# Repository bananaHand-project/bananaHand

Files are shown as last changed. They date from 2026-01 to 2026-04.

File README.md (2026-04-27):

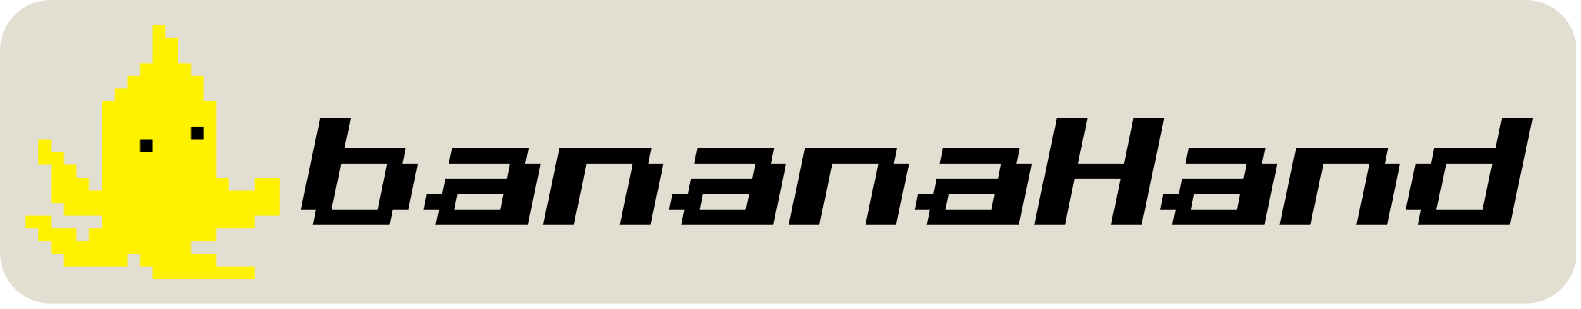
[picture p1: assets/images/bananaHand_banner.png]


---

**BananaHand** is an open-source 16 DOF/6 DOA humanoid hand designed for physical AI research and deployment on light-weight robot arms.

Hand teleop and telemetry demo

BananaHand features human-like proportions with no fore-arm, up to 4lb payload capacity, integrated palm and finger tip FSR based force sensing, and a low BOM cost of $900USD.

With the project being open-source as a top priority, all resources used in the creation are freely available and open-source themselves (KiCad, OnShape, Foxglove, Embassy-rs, etc.).

*We're in continuous development and actively seeking contributors, research partners, and company collaborators to shape the next generation of practical humanoid systems. Ready to join the future of open-source robotics?*

## Repo Structure

- [`docs/`](./docs/) contains build instructions, getting started guide, and more.
- [`firmware/`](./firmware/) contains the code that runs on the bananaHand main board.
  - [`firmware/primary-g474/`](./firmware/primary-g474/) contains the firmware run on the primary MCU (stm32g474).
  - [`firmware/sensing-c071/`](./firmware/sensing-c071/) contains the firmware run on the sensing MCU (stm32c071).
  - [`firmware/common/`](./firmware/common/) contains code used by both MCUs.
  - [`firmware/experiments/`](./firmware/experiments/) contains code used in the development of the hand.
- [`hardware/`](./hardware/) contains both electrical and mechanical CAD models, BOMs, and detailed descriptions.
- [`software/`](./software/) contains ROS and Foxglove implementations.

---
***We can't wait to see what you grasp!***

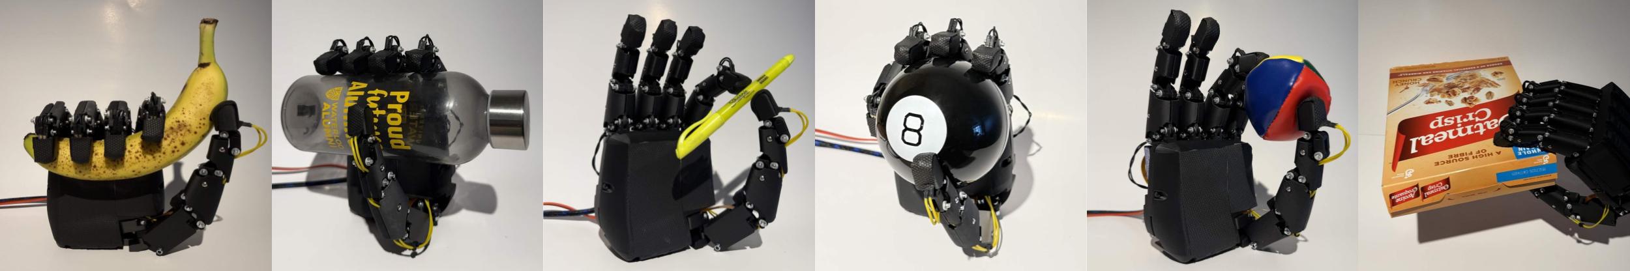
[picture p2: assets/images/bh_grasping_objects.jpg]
bananaHand grasping objects


Made with ❤️ in 🇨🇦 at 🪿.

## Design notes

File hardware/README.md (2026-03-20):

# Hardware

This folder contains files and information regarding CAD, PCB, BOM, and manufacturing files.

## CAD
The CAD for BananaHand is publicly hosted on Onshape for users to access, copy, and export. The link to the Onshape can be found below:
https://cad.onshape.com/documents/f31bf6b3693af5bdccd83d8c/w/d3ff086828b5bf32fd810037/e/c279298b7ecf651fc2ff6194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

## BOM and Assembly Guide
The BananaHand Bill of Materials can be found on Google Sheets through the following link: https://docs.google.com/spreadsheets/d/1iI2emtTwuQCvzfNIwKDL3XGDNOlOl9XfeF24zAXsmqI/edit?usp=sharing

The assembly guide for BananaHand can be found in the resources folder.

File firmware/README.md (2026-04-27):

# Firmware

Firmware for the BananaHand main board lives here. The board uses two MCUs:

- `stm32g474` (primary): communication, control loops, motor drive outputs.
- `stm32c071` (sensing): force sensor acquisition and streaming to the primary MCU.

## High-Level Architecture

- [`primary-g474/primary`](./primary-g474/primary): production firmware for the primary controller.
- [`sensing-c071`](./sensing-c071): production firmware for force sensing.
- [`common`](./common): shared packet definitions and encoding helpers.
- `experiments/`: one-off firmware targets used during bring-up and feature exploration.

## How It Works

1. The C071 samples 10 FSR channels (200 Hz), packs 12-bit readings with a checksum (`banana_hand_common::ForceDataPacket`), and sends them over UART to the G474.
2. The G474 runs concurrent Embassy tasks for host command RX (`USART3`), telemetry TX (`USART3`), force packet RX from C071 (`USART2`), position ADC sampling (`ADC1`), and current ADC sampling (`ADC2`).
3. A 200 Hz control loop on the G474 reads the latest shared snapshots and runs either `Position` mode (PID on actuator position) or `Force` mode (PID on force feedback where available).
4. Motor commands are converted to PWM outputs for the H-bridge channels.
5. Telemetry is sent to the host as combined position + force + current frames.

Current host communication is UART (`115200`) with COBS framing and a simple additive checksum on payloads.

## Build/Flash

Primary MCU (`STM32G474`):

```bash
cd firmware/primary-g474/primary
cargo run --release
```

Sensing MCU (`STM32C071`):

```bash
cd firmware/sensing-c071
cargo run --release
```

Both targets are configured to use `probe-rs run` in their local `.cargo/config.toml`.

## TODOs

- Add firmware support for CAN and half-duplex RS485 (board hardware already exposes both).
- Improve message passing robustness (stronger CRCs, sequence IDs with ACK/NACK or retries, and host heartbeat/command timeout fail-safe behavior).
- Remove unnecessary COBS usage (evaluate simpler framing on fixed-size links and delete stale code paths such as `sensing-c071/src/protocol.rs`).
- Tighten C071->G474 framing robustness (current stream has no explicit delimiter; resync is byte-sliding on checksum failure).
- Centralize protocol definitions so firmware and ROS bridge cannot drift.
- Create actuator/sensor calibration procedure (per-channel scaling and nonlinearity compensation).
- Add support for HRTIM triggered ADC conversions to `embassy-rs` so current feedback for protection and control (overcurrent limits, stall detection, fault handling).

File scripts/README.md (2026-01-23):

# Scripts

Utility scripts (calibration, flashing, logs).

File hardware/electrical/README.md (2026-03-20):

# Electrical

The electrical system for bananaHand is built around the main board. The main board is responsible for the following functions: communication with the controlling device, motor control, and FSR sensing. A simplified block diagram describing the main board can be seen below. It requires a single +12V 24W input source and exposes UART, CAN bus, and half-duplex RS485 options for interfacing. Depending on the device you are trying to interface with, a buck converter may be needed to drop your source voltage down to the required 12V.

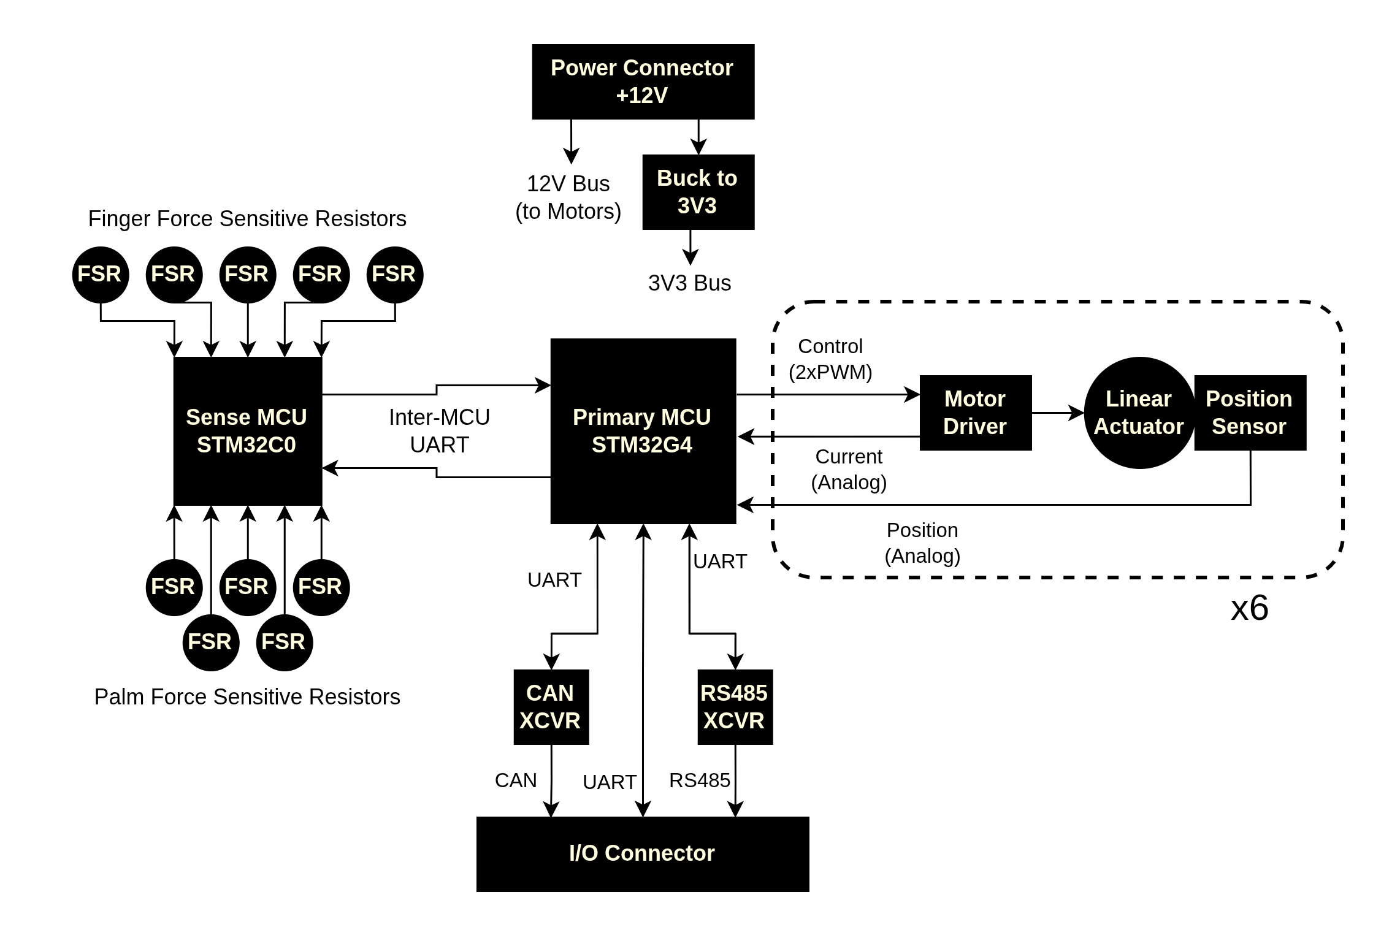
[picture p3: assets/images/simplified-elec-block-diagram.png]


## Main Board

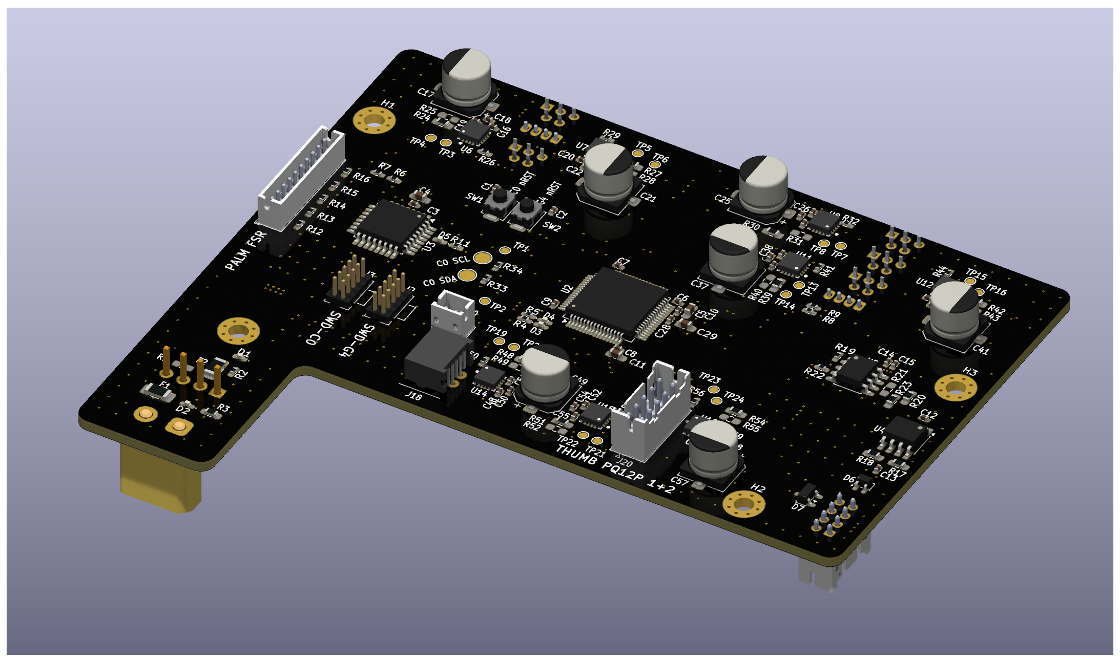
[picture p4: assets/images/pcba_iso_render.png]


The main board has the following sub-circuits:

- **Micro-controllers**: There are two MCUs on the main board. The first is the stm32g474, responsible for communication with the upstream device and motor control. The second micro-controller is the stm32c071, which acts as a "smart" ADC, filtering and forwarding force readings to the stm32g4.
- **Power stage**: Basic fuse protection, and a MPM3610 buck converter for 12V -> 3V3 for logic level ICs
- **Motor driving**: There are eight DRV8876 motor driver circuits for the [PQ12P](https://www.actuonix.com/pq12-30-12-p). The driving circuits are controlled and motor positions are read by the stm32g474 micro-controller.
- **Force sensing**: Simple linear voltage divider circuits are used to interface with the force sensitive resistors. Their voltages are read by the 2nd micro-controller on board the stm32c071
- **Communication interfaces**: There are three communication interfaces exposed by the board: CAN Bus, UART, and half-duplex RS485.

### Schematic

A full PDF of the schematic can be found in `bh_main_board/bananaHand_main_board_sch.pdf` or linked [here](./bh_main_board/bananaHand_main_board_sch.pdf).

### Layout

**Four layer:** Sig, GND, GND/PWR, Sig

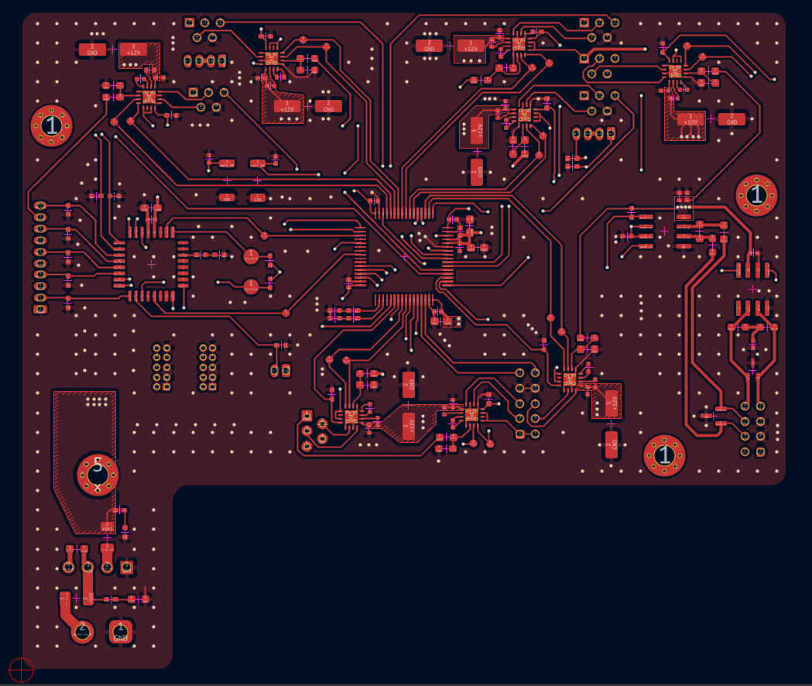
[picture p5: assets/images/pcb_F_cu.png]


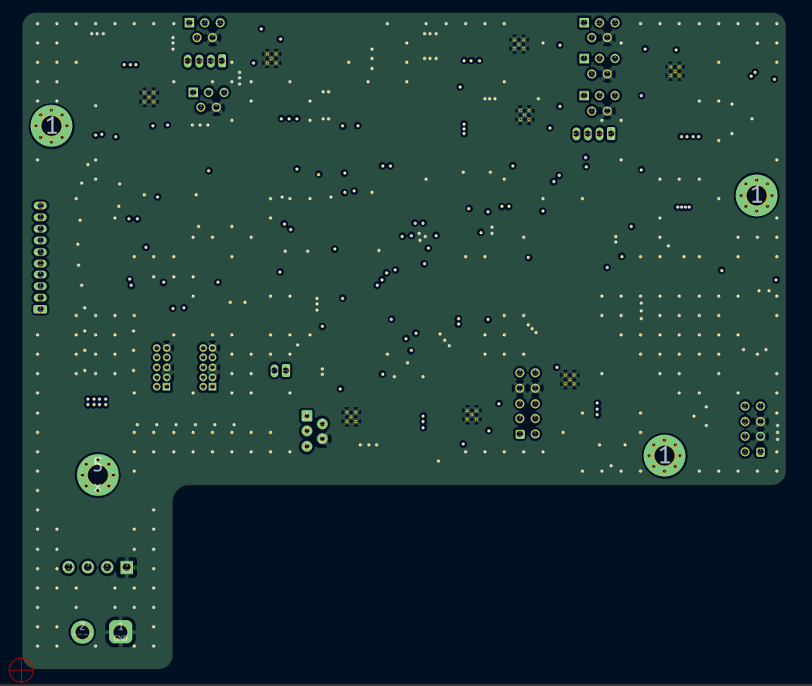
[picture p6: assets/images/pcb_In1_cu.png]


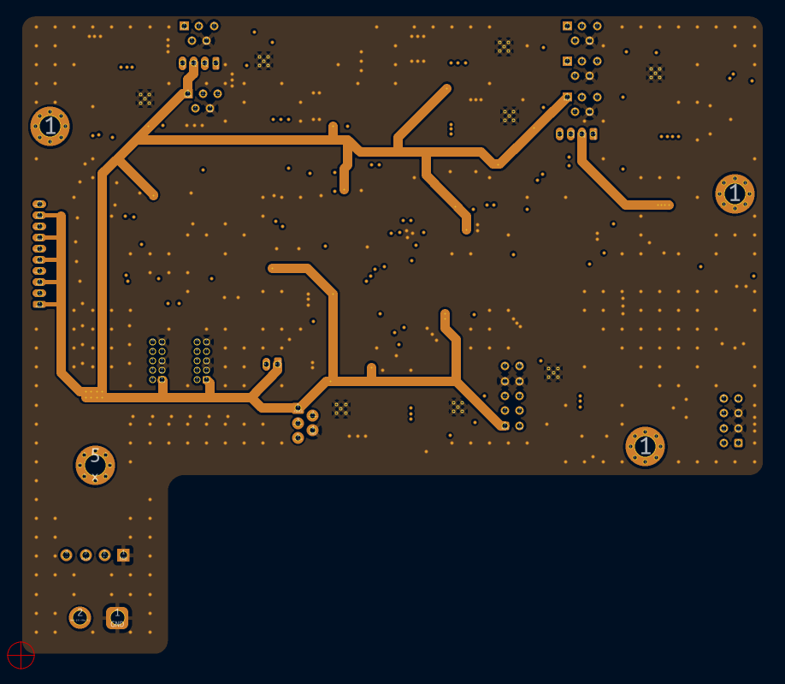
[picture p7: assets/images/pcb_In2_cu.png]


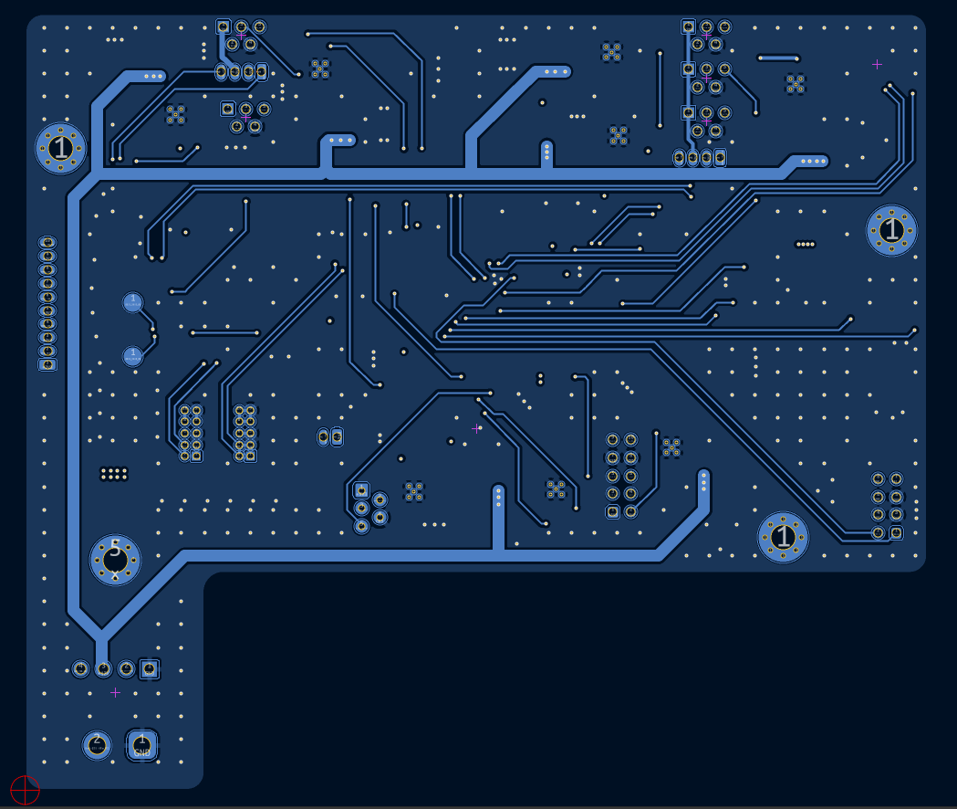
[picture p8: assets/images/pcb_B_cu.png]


### Known Flaws

#### V0.1.0

No issues that impact the performance of the board or require re-work.

- The silkscreen on the back labelling the PQ12P connectors for Index1 and Index 2 are flipped.
- Index 2 breaks the convention of the HRTIM channel connections to DRV8876 with `IN1 <-> CH1` and `IN2 <-> CH2` (instead of `IN1 <-> CH2` and `IN2 <-> CH1` like all other fingers).

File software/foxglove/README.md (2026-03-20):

# Foxglove Extensions

This folder contains custom Foxglove tooling for Banana Hand.

## Requirements
- Node.js 20+
- npm 10+

Check your versions:
```bash
node -v
npm -v
```

If you see an error like `Unexpected token '?'` during `foxglove-extension build`, your Node version is too old.

## Quick Start
Install the force-pad extension:
```bash
cd software/foxglove/banana-hand-force-heatmap
# optional if you use nvm:
# nvm use
npm install
npm run local-install
```

Then reload Foxglove, add `BananaHandForceHeatmap`, and set these in panel settings:
- `topic` for example `/rx_force`
- `dataIndex` for example `0`
- `title` for example `Thumb`

## Available Extensions
- `banana-hand-force-heatmap`
  custom panel for a single configurable force pad

## Build
Foxglove extensions require Node.js and npm.

Example:
```bash
cd software/foxglove/banana-hand-force-heatmap
# optional if you use nvm:
# nvm use
npm install
npm run local-install
```

After that, restart or reload the Foxglove desktop app and add the custom panel from the Add Panel menu.

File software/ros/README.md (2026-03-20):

# BananaHand ROS Bringup

## Quick Start
Build and run the full stack:
```bash
cd /home/lokesh/BananaHand/software/ros
source /opt/ros/humble/setup.bash
pip install --user -r requirements.txt
colcon build --symlink-install
source install/setup.bash
ros2 launch banana_bringup bringup.launch.py serial_port:=/dev/ttyACM0 baud:=115200
```

Visualization only:
```bash
cd /home/lokesh/BananaHand/software/ros
source /opt/ros/humble/setup.bash
source install/setup.bash
ros2 launch banana_hand_visualization mujoco_visualization.launch.py show_mujoco_viewer:=true
```

This workspace contains the ROS 2 stack for:
- hand tracking (`banana_hand_tracking`)
- hand mapping (`banana_hand_mapping`)
- serial hardware I/O (`banana_serial_bridge`)
- visualization and debugging (`banana_hand_visualization`)
- top-level bringup (`banana_bringup`)

The default end-to-end flow is:
- webcam + tracking publishes `/hand/teleop_joint_trajectory`
- mapping converts teleop ratios to `/tx_positions`
- serial bridge exchanges `/tx_positions`, `/rx_positions`, `/rx_force`, and `/rx_current` with hardware
- visualization publishes simulated joint state and filtered debug topics for MuJoCo and Foxglove

## Build
```bash
cd software/ros
source /opt/ros/humble/setup.bash
pip install --user -r requirements.txt
colcon build --symlink-install --packages-select \
  banana_interfaces banana_hand_tracking banana_hand_mapping \
  banana_serial_bridge banana_hand_visualization banana_bringup
source install/setup.bash
```

Optional Foxglove bridge:
```bash
sudo apt install ros-$ROS_DISTRO-foxglove-bridge
```

## Run Full Bringup
```bash
ros2 launch banana_bringup bringup.launch.py \
  serial_port:=/dev/ttyACM0 baud:=115200
```

Useful variants:
```bash
# Disable the OpenCV preview window
ros2 launch banana_bringup bringup.launch.py show_preview:=false

# Launch the desktop MuJoCo viewer too
ros2 launch banana_bringup bringup.launch.py show_mujoco_viewer:=true

# Drive the visualization from teleop instead of rx_positions
ros2 launch banana_bringup bringup.launch.py \
  show_mujoco_viewer:=true state_source:=teleop

# Skip the visualization package entirely
ros2 launch banana_bringup bringup.launch.py include_visualization:=false

# Skip vision and mapping, keep serial + visualization
ros2 launch banana_bringup bringup.launch.py \
  include_vision:=false include_mapping:=false
```

Bringup launch arguments:
- `serial_port` default `/dev/ttyACM0`
- `baud` default `115200`
- `include_vision` default `true`
- `include_mapping` default `true`
- `include_visualization` default `true`
- `show_preview` default `true`
- `show_mujoco_viewer` default `false`
- `state_source` default `rx_positions`
- `show_fsr_debugger` default `false`
- `launch_foxglove_bridge` default `true`

## Run Visualization Separately
Launch the visualization stack by itself:
```bash
cd software/ros
source /opt/ros/humble/setup.bash
source install/setup.bash
ros2 launch banana_hand_visualization mujoco_visualization.launch.py
```

Common variants:
```bash
# Open the desktop MuJoCo viewer
ros2 launch banana_hand_visualization mujoco_visualization.launch.py \
  show_mujoco_viewer:=true

# Drive the visualization from tracking output instead of rx_positions
ros2 launch banana_hand_visualization mujoco_visualization.launch.py \
  state_source:=teleop show_mujoco_viewer:=true

# Disable Foxglove bridge startup
ros2 launch banana_hand_visualization mujoco_visualization.launch.py \
  launch_foxglove_bridge:=false
```

## Run Hand Tracking Separately
Combined webcam + tracking:
```bash
cd software/ros
source /opt/ros/humble/setup.bash
source install/setup.bash
ros2 launch banana_hand_tracking vision_teleop.launch.py
```

Tracking-only node:
```bash
ros2 launch banana_hand_tracking hand_tracking.launch.py
```

Webcam-only node:
```bash
ros2 launch banana_hand_tracking webcam.launch.py
```

## Foxglove
The visualization package publishes:
- `/banana_hand/mujoco_joint_states` (`sensor_msgs/msg/JointState`)
- `/banana_hand/force_state` (`sensor_msgs/msg/JointState`)
- `/banana_hand/current_state` (`sensor_msgs/msg/JointState`)

If `foxglove_bridge` is installed, `mujoco_visualization.launch.py` or `bringup.launch.py` can start it automatically.

Suggested Foxglove panels:
1. Plot `/banana_hand/mujoco_joint_states`
2. Plot `/banana_hand/force_state`
3. Plot `/banana_hand/current_state`

Use the desktop MuJoCo viewer for the 3D hand view.

## Quick Checks
```bash
ros2 service call /hand/calibrate std_srvs/srv/Trigger {}
ros2 topic hz /hand/teleop_joint_trajectory
ros2 topic echo /tx_positions
ros2 topic echo /rx_positions
ros2 topic echo /rx_force
ros2 topic echo /banana_hand/mujoco_joint_states
```

## Package Notes
- `banana_hand_tracking`: webcam capture and MediaPipe-based teleop tracking
- `banana_hand_mapping`: converts teleop ratios to actuator-scale command values
- `banana_serial_bridge`: hardware transport for position, force, and current topics
- `banana_hand_visualization`: MuJoCo state publisher, desktop viewer integration, Foxglove-facing debug topics, and FSR debug GUI

Each package README documents its own node parameters and launch usage.

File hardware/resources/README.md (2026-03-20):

# Resources

Assembly guide and other resources

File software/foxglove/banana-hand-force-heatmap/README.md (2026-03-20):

# Banana Hand Force Heatmap

Custom Foxglove panel extension for visualizing one force value as a compact heat pad.

The panel is designed for:
- raw `/rx_force` array-style messages
- `/banana_hand/force_state`

The topic is selected from the normal Foxglove panel settings sidebar rather than being hardcoded.
Each panel instance lets you choose:
- the source topic
- the array or position index to read
- the panel title
- the min/max color scale

For raw `/rx_force`, the panel reads `message.data` and maps the 10 array values in this order:
- `0` `thumb`
- `1` `index`
- `2` `middle`
- `3` `ring`
- `4` `pinky`
- `5` `palm_1`
- `6` `palm_2`
- `7` `palm_3`
- `8` `palm_4`
- `9` `palm_5`

## What It Shows
- one configurable force value per panel instance

## Install
Foxglove custom panels require Node.js. Foxglove’s docs currently recommend using the extension tooling and then running `npm run local-install` to copy the built extension into your local Foxglove extensions folder. Sources:
- https://docs.foxglove.dev/docs/extensions
- https://docs.foxglove.dev/docs/extensions/local-development
- https://docs.foxglove.dev/docs/extensions/guides/create-custom-panel

On a machine with Node and npm installed:
```bash
cd /home/lokesh/BananaHand/software/foxglove/banana-hand-force-heatmap
npm install
npm run local-install
```

Then restart or reload Foxglove and add the `BananaHandForceHeatmap` panel from the Add Panel menu.

If `npm install` fails, make sure the package versions match Foxglove's current extension toolchain. This project is pinned to:
- `@foxglove/extension` `^2.35.0`
- `create-foxglove-extension` `^1.0.6`

This project's `local-install` script currently maps to:
```bash
npm run build && foxglove-extension install
```

## Use
Start the Banana Hand visualization stack:
```bash
cd /home/lokesh/BananaHand/software/ros
source /opt/ros/humble/setup.bash
source install/setup.bash
ros2 launch banana_hand_visualization mujoco_visualization.launch.py
```

Then in Foxglove:
1. Connect to the Foxglove bridge
2. Add `BananaHandForceHeatmap`
3. Open the panel settings and choose:
   - `/rx_force`
   - the `dataIndex` you want, for example `0` through `9`
   - a custom title, for example `Thumb Tip`
4. Duplicate the panel if you want multiple pads in one layout

Example layout:
- one pad for `thumb`
- one pad for `index`
- one pad for `middle`
- one pad for `ring`
- one pad for `pinky`
- one pad each for `palm_1` through `palm_5`

## Layout Suggestion
For a nice default debugging layout:
- one row of 5 small fingertip pads
- one row of 5 small palm pads
- optional Plot panel for all `/rx_force` values
- optional Raw Messages panel on `/rx_force`

## Notes
- This repo currently does not have `node` or `npm` installed in the checked environment, so the extension source was scaffolded but not built locally here.
- The panel topic is configured in Foxglove panel settings.
- The displayed value comes from `message.data[dataIndex]` for raw `/rx_force`.
- The color scale is adjustable in panel settings through `min` and `max`.

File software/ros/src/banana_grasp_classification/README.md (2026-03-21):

# banana_grasp_classification

Point-cloud preprocessing and rule-based grasp classification for BananaHand.

This package contains three ROS 2 nodes:
- `ground_plane_removal_node`
- `grasp_rule_classifier_node`
- `scan_grasp_pipeline_node`

It also contains two convenience launch files:
- `grasp_pipeline.launch.py`
- `scan_to_grasp.launch.py`

The intended workflow is:
1. start from a reconstructed downsampled object cloud
2. remove the table / ground plane when one is detectable
3. classify the remaining object cloud into an initial grasp type
4. save both the processed `.ply` and a detailed grasp JSON beside it

The scan-to-grasp path keeps the existing one-shot tools intact:
- `banana_3d_reconstruction/object_scan_node` still captures and saves the scan folder
- `scan_grasp_pipeline_node` listens for each completed scan folder, runs ground removal, runs classification, then publishes the selected grasp/opening as a typed ROS topic

## Reference Results

The scan/result set used during classifier testing is stored in:
- `resource/banana_scans`

Those folders mirror the test objects we ran through the pipeline and keep the saved outputs beside each scan, including:
- ground-removed `.ply` clouds
- grasp-classification `.json` results

## Nodes

### `ground_plane_removal_node`

This node searches an input directory for a reconstructed point cloud, fits candidate support planes with RANSAC on a downsampled copy, scores those candidates using:
- inlier ratio
- alignment with the configured height axis
- whether the plane lies toward the expected table side of the cloud

If a valid table-like plane is found, the node:
- keeps only points on the object side of that plane
- applies DBSCAN cluster filtering
- optionally applies statistical outlier removal
- writes `<input_stem>_ground_removed.ply`

If no valid table-like plane is found, the node does not fail the pipeline anymore. It writes an unchanged passthrough copy using the same output suffix so downstream classification can still run.

Supported input filenames:
- `final_output_cloud_downsampled.ply`
- `final_object_cloud_downsampled.ply`

Default output filename:
- `final_object_cloud_downsampled_ground_removed.ply`

### `grasp_rule_classifier_node`

This node searches for an already ground-removed cloud, computes geometric descriptors, runs a deterministic scored rules engine, writes a JSON result beside the cloud, and exits.

Supported input filenames by default:
- `final_output_cloud_downsampled_ground_removed.ply`
- `final_object_cloud_downsampled_ground_removed.ply`

Default output filename:
- `final_object_cloud_downsampled_ground_removed_grasp.json`

The classifier is rule-based only. It does not use ML inference.

Grip classes:
- `pinch`
- `tripod`
- `cylindrical`
- `spherical`
- `hook`

`hook` remains in the output but is strongly suppressed with an explicit penalty so it almost never wins unless the evidence is unusually strong.

### `scan_grasp_pipeline_node`

This node subscribes to the completed-scan directory topic from `banana_3d_reconstruction`, then runs:
1. `ground_plane_removal_node`
2. `grasp_rule_classifier_node`

After the grasp JSON is written, it publishes:
- `/grasp_classification/recommendation` (`banana_interfaces/msg/GraspRecommendation`)

Message fields:
- `selected_grip`
- `recommended_opening_m`

### `grasp_executor`

This node subscribes to:
- `/grasp_classification/recommendation` (`banana_interfaces/msg/GraspRecommendation`)
- `/grasp_classification/execute_grasp` (`std_msgs/msg/Empty`)
- `/grasp_classification/release` (`std_msgs/msg/Empty`)

It publishes:
- `/tx_positions` (`std_msgs/msg/UInt16MultiArray`)

Behavior:
- caches the latest command derived from `selected_grip` and `recommended_opening_m`
- waits for an execute trigger before publishing that cached command
- publishes the open pose and clears the cached grasp when a release trigger arrives
- keeps thumb revolve at the grip-specific preset
- linearly interpolates the other actuators from an "open" pose at `0.15 m` to the full grip pose at `0.03 m`
- clamps openings outside that range to the nearest endpoint

By default it listens on:
- `/object_scan/completed_scan_dir` (`std_msgs/msg/String`)

## Classifier Behavior

The classifier is designed for partial single-view RealSense object clouds. It uses:
- conservative statistical cleanup
- optional radius outlier cleanup
- robust PCA extents using percentiles
- oriented bounding box extents
- normal reuse or adaptive estimation
- local surface variation as a direct flat-vs-curved surface cue
- normal-direction concentration
- trimmed cylinder fitting
- least-squares sphere fitting with a centroid-offset sanity check
- explicit box-like vs cylinder-like vs sphere-like intermediate evidence
- explicit per-grip score terms saved into JSON

Additional classifier details reflected in the current code:
- `surface_variation_median` plays a direct role in separating flat box faces from curved cylindrical or spherical surfaces
- `normal_estimation_radius_m` is an upper-bound cap, not a fixed radius; the actual radius is scaled from the object's minor extent
- sphere fits that drift too far from the cloud centroid are rejected so partial hemispheres do not create unrealistic large sphere diameters
- compact round objects use an explicit small-sphere cue so ping-pong-ball-scale objects favor `tripod` instead of falling through to `pinch`
- larger round objects require both strong round-fit evidence and size before `spherical` gets boosted
- cylindrical power grasps get extra support from tall curved bodies, while medium / large box-like prisms still map to `cylindrical`
- `pinch` depends on a genuinely small usable body span, not just a tiny shell depth, so wide hollow objects like cups do not collapse to precision grasps
- compact non-spherical objects with both small height and small width get an explicit `pinch` boost, which helps cases like small rounded cases that are not truly spherical
- `small_body_dimension_max_m` defaults to `0.06`, and is used as the explicit body-size split for the compact-object rules
- sphere-like objects with curved surfaces, similar height/width, and both dimensions below that 6 cm split get an explicit `tripod` boost
- sphere-like objects with curved surfaces and both height/width at or above that 6 cm split get extra support for `spherical`
- non-spherical objects whose visible width and thickness both stay below that 6 cm split get an explicit `pinch` boost, which keeps thin small cylinders and compact cases out of wrap grasps
- mildly taller-than-wide round shells that are large enough for a wrap grasp but not sphere-dominant get an extra cylindrical bias, which keeps cups and similar hollow objects from being treated as spheres
- tall curved bodies whose height is noticeably larger than their width lose spherical support and gain cylindrical support, which keeps cups and similar objects from being treated as spheres
- when that tall curved-body rule wins, the cylindrical opening uses the visible cylindrical diameter span instead of the sphere-fit diameter
- the JSON output intentionally keeps the `single_view_partial_cloud` assumption enabled for this capture pipeline

Important practical behavior:
- large cereal box / Lego box -> usually `cylindrical` using a thickness-like span
- bottle / mug / spray bottle / olive oil bottle -> usually `cylindrical`
- orange / apple -> usually `spherical` if large enough
- ping pong ball / lime -> usually `tripod`
- glue stick / small box / dice -> usually `pinch`

The recommended opening is:
- `recommended_opening_m = grasp_span_basis_m + opening_margin_m`
- for round-like `cylindrical` or `spherical` grasps, `grasp_span_basis_m` uses the cloud's `width_like` span by default
- box-like power grasps still keep their existing thickness-like span logic

By default:
- `opening_margin_m = 0.03`

If `max_hand_opening_m > 0`, the final opening is clamped.

## Build

```bash
cd /home/dbhaumik/BananaHand/software/ros
source /opt/ros/humble/setup.bash
colcon build --symlink-install --packages-select \
  banana_interfaces banana_3d_reconstruction banana_grasp_classification
source install/setup.bash
```

## Run Ground Plane Removal

```bash
ros2 run banana_grasp_classification ground_plane_removal_node --ros-args \
  -p input_dir:=/home/dbhaumik/banana_scans/cup
```

Useful ground-removal parameters:
- `input_dir`: directory to search
- `recursive_search`: whether to search subdirectories, default `true`
- `output_suffix`: output stem suffix, default `_ground_removed`
- `ground_height_axis`: axis treated as height, one of `x`, `y`, `z`
- `table_is_positive_direction_along_axis`: whether the table is toward the positive direction of that axis
- `min_ground_axis_alignment`: minimum normal alignment with the chosen axis
- `voxel_size_m`: downsampling used only for plane fitting
- `plane_distance_threshold_m`: RANSAC inlier threshold
- `plane_ransac_n`
- `plane_num_iterations`
- `max_ground_plane_candidates`
- `min_plane_inlier_ratio`
- `plane_clearance_above_table_m`: clearance margin above the detected table plane
- `remove_statistical_outliers`
- `sor_nb_neighbors`
- `sor_std_ratio`
- `cluster_eps_m`
- `cluster_min_points`
- `min_cluster_size`
- `keep_largest_cluster_only`

Notes:
- if no valid plane is found, the node writes a passthrough copy and returns success
- if DBSCAN rejects everything, the node keeps the current cloud instead of destroying it

## Run Rule-Based Grasp Classification

```bash
ros2 run banana_grasp_classification grasp_rule_classifier_node --ros-args \
  -p input_dir:=/home/dbhaumik/banana_scans/cup
```

Useful classifier parameters:
- `input_dir`: directory to search
- `recursive_search`: whether to search subdirectories, default `true`
- `ground_removed_suffix`: required suffix for the classifier input, default `_ground_removed`
- `output_suffix`: JSON output suffix, default `_grasp`
- `opening_margin_m`
- `max_hand_opening_m`
- `small_object_max_span_m`
- `tripod_object_max_span_m`
- `power_grasp_min_span_m`
- `small_body_dimension_max_m`
- `spherical_extent_ratio_max`
- `spherical_fit_error_max_m`
- `cylindrical_radius_cv_max`
- `cylindrical_fit_error_max_m`
- `box_flatness_ratio_max`
- `box_power_grasp_min_major_m`
- `box_power_grasp_min_middle_m`
- `hook_score_penalty`

Cleanup and descriptor parameters:
- `statistical_nb_neighbors`
- `statistical_std_ratio`
- `radius_outlier_nb_points`
- `radius_outlier_radius_m`
- `use_radius_outlier_filter`
- `extent_percentile_low`
- `extent_percentile_high`
- `surface_variation_k_neighbors`
- `normal_estimation_radius_m`: upper cap for adaptive normal estimation radius
- `normal_estimation_max_nn`
- `cylinder_axis_trim_percent`
- `cylinder_radial_outlier_percent`
- `sphere_fit_inlier_percentile`

Note:
- this list is for running `grasp_rule_classifier_node` directly
- `scan_grasp_pipeline_node` and `scan_to_grasp.launch.py` currently forward only:
  `opening_margin_m`, `max_hand_opening_m`, `small_object_max_span_m`,
  `tripod_object_max_span_m`, and `power_grasp_min_span_m`
- parameters like `small_body_dimension_max_m` still use the classifier's built-in default when you run the end-to-end scan-to-grasp launch

## Combined Launch Pipeline

`grasp_pipeline.launch.py` runs ground removal first and then classification in one launch command.

```bash
ros2 launch banana_grasp_classification grasp_pipeline.launch.py \
  input_dir:=/home/dbhaumik/banana_scans/cup
```

Exposed launch arguments:
- `input_dir`
- `recursive_search`
- `output_suffix`: ground-removal suffix, default `_ground_removed`
- `classifier_output_suffix`: classifier JSON suffix, default `_grasp`
- `opening_margin_m`
- `max_hand_opening_m`
- `small_object_max_span_m`
- `tripod_object_max_span_m`
- `power_grasp_min_span_m`

Behavior:
- if ground removal finds a table-like plane, the classifier uses the filtered cloud
- if ground removal does not find a valid plane, the classifier still runs on the passthrough `_ground_removed.ply`

## End-to-End Scan To Grasp

`scan_to_grasp.launch.py` starts the scan node and automatically runs ground removal plus grasp classification after each completed scan.

Unlike `grasp_pipeline.launch.py`, this launch is meant to stay running until the operator stops it. You can keep the launch open and repeatedly trigger new scans with:

```bash
ros2 service call /object_scan/start_scan std_srvs/srv/Trigger "{}"
```

Each successful scan save publishes a new scan directory on `/object_scan/completed_scan_dir`, and the full post-processing pipeline runs again for that new scan.

```bash
ros2 launch banana_grasp_classification scan_to_grasp.launch.py
```

Useful overrides:

```bash
ros2 launch banana_grasp_classification scan_to_grasp.launch.py \
  output_dir:=/tmp/banana_scans \
  show_preview:=true \
  enable_roi_selection:=true \
  result_topic:=/grasp_classification/recommendation
```

Exposed launch arguments:
- `params_file`
- `show_preview`
- `enable_roi_selection`
- `device_serial`
- `output_dir`
- `result_topic`
- `ground_removed_suffix`
- `classifier_output_suffix`
- `opening_margin_m`
- `max_hand_opening_m`
- `small_object_max_span_m`
- `tripod_object_max_span_m`
- `power_grasp_min_span_m`

These are the only classifier-threshold arguments currently exposed through the end-to-end launch. Other classifier parameters, including `small_body_dimension_max_m`, are not forwarded by `scan_grasp_pipeline_node` right now and therefore stay at their node defaults during `scan_to_grasp.launch.py`.

Behavior:
- when `/object_scan/start_scan` finishes successfully, the scan node saves the usual `.ply` and metadata files
- when ROI selection is enabled, the preview starts with a full-frame ROI and you can drag a box so only depth points inside that ROI feed the scan
- the scan node then publishes the saved scan directory on `/object_scan/completed_scan_dir`
- `scan_grasp_pipeline_node` immediately runs the same ground-removal and classification executables used by the manual pipeline
- after the grasp JSON is saved, the pipeline node publishes `/grasp_classification/recommendation`

## JSON Output

The classifier writes:
- `<input_stem>_grasp.json`

The JSON is intentionally verbose and includes:
- selected grip
- confidence
- recommended opening
- grasp span basis
- all grip scores
- intermediate family evidence
- object family label
- decision path
- per-grip score terms
- PCA and OBB dimensions
- cylinder and sphere fit metrics
- local surface descriptors
- point cloud cleanup statistics
- assumptions used by the classifier
- parameter values used to produce the result

Example output pair:
- `final_object_cloud_downsampled_ground_removed.ply`
- `final_object_cloud_downsampled_ground_removed_grasp.json`

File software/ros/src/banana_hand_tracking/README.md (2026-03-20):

# Banana Hand Tracking

`banana_hand_tracking` contains the webcam capture and MediaPipe-based tracking nodes that produce hand landmarks and teleop joint ratios.

## Install
```bash
cd /home/lokesh/BananaHand/software/ros
source /opt/ros/humble/setup.bash
pip install --user -r requirements.txt
colcon build --symlink-install --packages-select banana_interfaces banana_hand_tracking
source install/setup.bash
```

## Run
Combined webcam + tracking:
```bash
ros2 launch banana_hand_tracking vision_teleop.launch.py
```

Tracking only:
```bash
ros2 launch banana_hand_tracking hand_tracking.launch.py
```

Webcam only:
```bash
ros2 launch banana_hand_tracking webcam.launch.py
```

## Topics and Service
- `/camera/image_raw` (`sensor_msgs/msg/Image`)
- `/hand/landmarks` (`banana_interfaces/msg/HandState`)
- `/hand/teleop_joint_trajectory` (`trajectory_msgs/msg/JointTrajectory`)
- `/hand/calibrate` (`std_srvs/srv/Trigger`)

## Launch Files
`webcam.launch.py`
- starts `webcam_node`
- fixed parameters in the launch file:
  - `camera_index=0`
  - `frame_id=camera`
  - `publish_hz=30.0`

`hand_tracking.launch.py`
- starts `hand_tracking_node`
- fixed parameters in the launch file:
  - `input_topic=/camera/image_raw`
  - `frame_id=camera`
  - `show_preview=true`

`vision_teleop.launch.py`
- starts both `webcam_node` and `hand_tracking_node`
- launch arguments:
  - `show_preview` default `true`

## Webcam Node Parameters
`webcam_node` supports:
- `camera_index`
  default `0`
- `frame_id`
  default `camera`
- `publish_hz`
  default `30.0`
- `show_preview`
  default `true`
- `use_v4l2`
  default `true`

Example:
```bash
ros2 run banana_hand_tracking webcam_node --ros-args \
  -p camera_index:=1 \
  -p show_preview:=false
```

## Hand Tracking Node Parameters
`hand_tracking_node` supports:
- `input_topic`
  default `/camera/image_raw`
- `frame_id`
  default `camera`
- `show_preview`
  default `true`
- `mirror_handedness`
  default `true`
- `alpha`
  default `0.2`
- `process_width`
  default `640`
- `process_height`
  default `480`
- `preview_fps`
  default `15.0`
- `process_fps`
  default `0.0`
  `0.0` means uncapped processing

Example:
```bash
ros2 run banana_hand_tracking hand_tracking_node --ros-args \
  -p input_topic:=/camera/image_raw \
  -p alpha:=0.15 \
  -p process_width:=640 \
  -p process_height:=480
```

## Calibration
```bash
ros2 service call /hand/calibrate std_srvs/srv/Trigger {}
```

## Quick Checks
```bash
ros2 node info /webcam_node
ros2 node info /hand_tracking_node
ros2 topic hz /camera/image_raw
ros2 topic hz /hand/landmarks
ros2 topic hz /hand/teleop_joint_trajectory
```

## Troubleshooting
- If `/camera/image_raw` exists but no frames arrive, try a different `camera_index`
- If another app is using the webcam, close it before launching tracking
- If `/dev/video0` does not exist on your machine, use a node run command and override `camera_index`

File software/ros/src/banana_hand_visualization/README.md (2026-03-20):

# Banana Hand Visualization

`banana_hand_visualization` is the ROS 2 visualization package for the Banana Hand system.

It contains:
- the main visualization node that drives MuJoCo state from live ROS topics
- optional desktop MuJoCo viewing
- Foxglove-facing debug topics
- the FSR debug GUI and test publisher

## Install
```bash
cd /home/lokesh/BananaHand/software/ros
source /opt/ros/humble/setup.bash
pip install --user -r requirements.txt
colcon build --symlink-install --packages-select banana_hand_visualization
source install/setup.bash
```

Optional Foxglove bridge:
```bash
sudo apt install ros-$ROS_DISTRO-foxglove-bridge
```

## Run
Launch the visualization stack:
```bash
ros2 launch banana_hand_visualization mujoco_visualization.launch.py
```

Useful variants:
```bash
# Open the desktop MuJoCo viewer too
ros2 launch banana_hand_visualization mujoco_visualization.launch.py \
  show_mujoco_viewer:=true

# Drive MuJoCo from teleop tracking instead of rx_positions
ros2 launch banana_hand_visualization mujoco_visualization.launch.py \
  state_source:=teleop show_mujoco_viewer:=true

# Do not start Foxglove bridge from the launch file
ros2 launch banana_hand_visualization mujoco_visualization.launch.py \
  launch_foxglove_bridge:=false
```

Standalone viewer only:
```bash
ros2 run banana_hand_visualization standalone_viewer
```

## Topics
Subscriptions:
- `/rx_positions` (`sensor_msgs/msg/JointState`)
- `/hand/teleop_joint_trajectory` (`trajectory_msgs/msg/JointTrajectory`)
- `/rx_force` (`std_msgs/msg/UInt16MultiArray`)
- `/rx_current` (`sensor_msgs/msg/JointState`)

Publications:
- `/banana_hand/mujoco_joint_states` (`sensor_msgs/msg/JointState`)
- `/banana_hand/force_state` (`sensor_msgs/msg/JointState`)
- `/banana_hand/current_state` (`sensor_msgs/msg/JointState`)

`/banana_hand/force_state` is published in this order:
- `thumb`
- `index`
- `middle`
- `ring`
- `pinky`
- `palm_1`
- `palm_2`
- `palm_3`
- `palm_4`
- `palm_5`

## Launch Arguments
`mujoco_visualization.launch.py` supports:
- `show_mujoco_viewer` default `false`
- `state_source` default `rx_positions`
- `launch_foxglove_bridge` default `true`

## Main Visualization Node Parameters
The `mujoco_visualizer` node supports:

- `model_path`
  default `/share/banana_hand_visualization/mujoco/scene.xml` inside the installed package
- `state_publish_rate_hz`
  default `30.0`
- `show_mujoco_viewer`
  default `false`
- `state_source`
  default `rx_positions`
  options: `rx_positions`, `teleop`
- `teleop_topic`
  default `/hand/teleop_joint_trajectory`
- `feedback_topic`
  default `/rx_positions`
- `teleop_input_min_ratio`
  default `0.0`
- `teleop_input_max_ratio`
  default `1.0`
- `teleop_source_indices`
  default `[0, 1, 2, 3, 4, 5, -1, -1]`
- `teleop_fill_ratio`
  default `0.0`
- `force_input_topic`
  default `/rx_force`
- `current_input_topic`
  default `/rx_current`
- `joint_state_topic`
  default `/banana_hand/mujoco_joint_states`
- `force_state_topic`
  default `/banana_hand/force_state`
- `current_state_topic`
  default `/banana_hand/current_state`
- `force_sensor_indices`
  default `[0, 1, 2, 3, 4, 5, 6, 7, 8, 9]`
- `force_scale`
  default `1.0`
- `current_filter_window`
  default `10`
- `actuator_map`
  default `["indexpiston", "middlepiston", "ringpiston", "pinkypiston", "thumbpiston", "tmpiston", "", ""]`
- `direct_joint_map`
  default `["", "", "", "", "", "", "indexrev4", "thumbrev4"]`
- `motor_mins`
  default `[400, 400, 400, 400, 300, 150, 0, 0]`
- `motor_maxs`
  default `[3900, 3900, 3900, 3900, 3900, 3900, 4095, 4095]`
- `position_invert_mask`
  default `[true, true, true, true, true, true, false, false]`
  order: `index_1, middle, ring, pinky, thumb_1, thumb_2, index_2, thumb_3`

Example:
```bash
ros2 run banana_hand_visualization mujoco_visualizer --ros-args \
  -p state_source:=teleop \
  -p show_mujoco_viewer:=true \
  -p position_invert_mask:="[true, true, true, true, true, true, false, false]"
```

## FSR Debug GUI
Run against live data:
```bash
ros2 run banana_hand_visualization fsr_visualizer
```

Launch with a synthetic publisher:
```bash
ros2 launch banana_hand_visualization fsr_visualizer_test.launch.py
```

Run only the synthetic publisher:
```bash
ros2 run banana_hand_visualization fsr_visualizer_test_publisher
```

FSR GUI parameters:
- `topic_name`
  default `rx_force`
- `finger_indices`
  default `[0, 1, 2, 3, 4]`
- `alpha`
  default `0.25`
- `global_min`
  default `0.0`
- `global_max`
  default `1023.0`
- `per_finger_min`
  default `[]`
- `per_finger_max`
  default `[]`
- `refresh_hz`
  default `30.0`
- `contact_threshold`
  default `0.7`
- `simulate_if_no_data`
  default `false`

Example:
```bash
ros2 run banana_hand_visualization fsr_visualizer --ros-args \
  -p topic_name:=rx_force \
  -p finger_indices:="[0, 2, 4, 6, 8]" \
  -p alpha:=0.35
```

## Foxglove
If `foxglove_bridge` is installed, the visualization launch file can start it automatically.

Suggested panels:
1. Plot `/banana_hand/mujoco_joint_states`
2. Plot `/banana_hand/force_state`
3. Plot `/banana_hand/current_state`

Use the desktop MuJoCo viewer for 3D hand motion rather than Foxglove markers.

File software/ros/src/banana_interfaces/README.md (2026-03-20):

# banana_interfaces

Custom message definitions for BananaHand.

Structure
- `msg/` for `.msg` files

Current messages
- `HandState.msg`
- `GraspRecommendation.msg`

`GraspRecommendation.msg` fields
- `string selected_grip`
- `float64 recommended_opening_m`

Notes
- Add new messages to `CMakeLists.txt` in the `msg_files` list.
- When you add messages, run `colcon build` to generate interfaces.

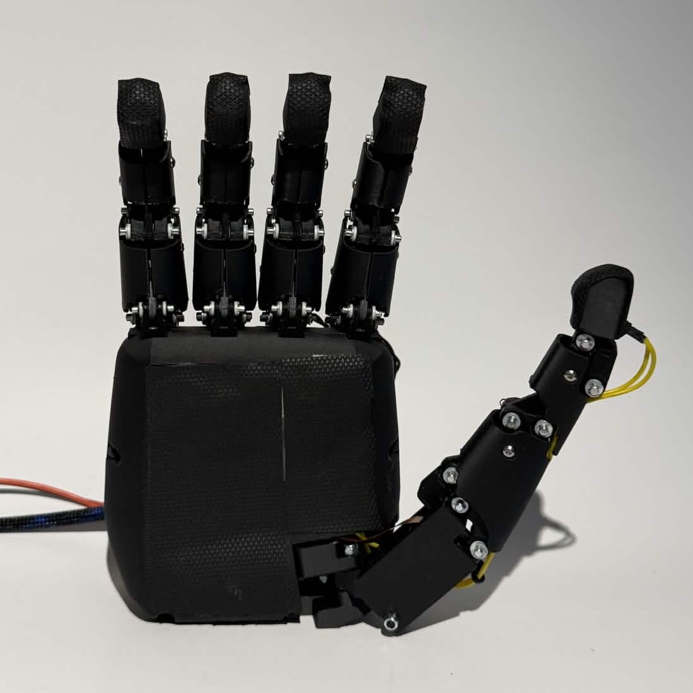
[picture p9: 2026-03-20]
assets/images/bh_open_palm.jpg

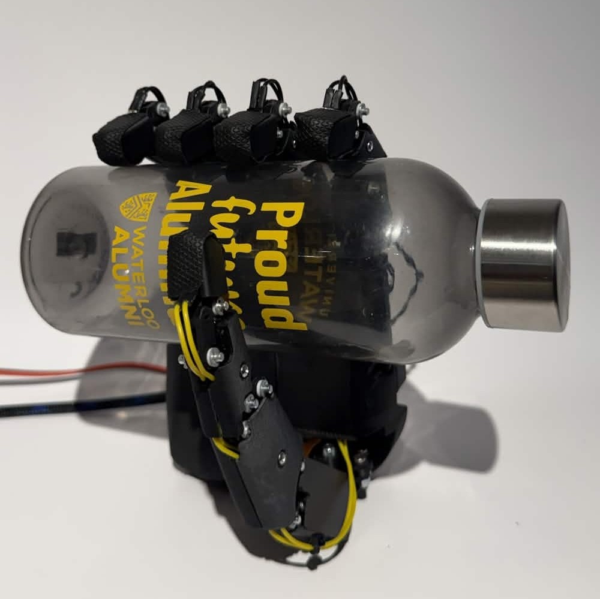
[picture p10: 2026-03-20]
assets/images/bh_holding_bottle.jpg

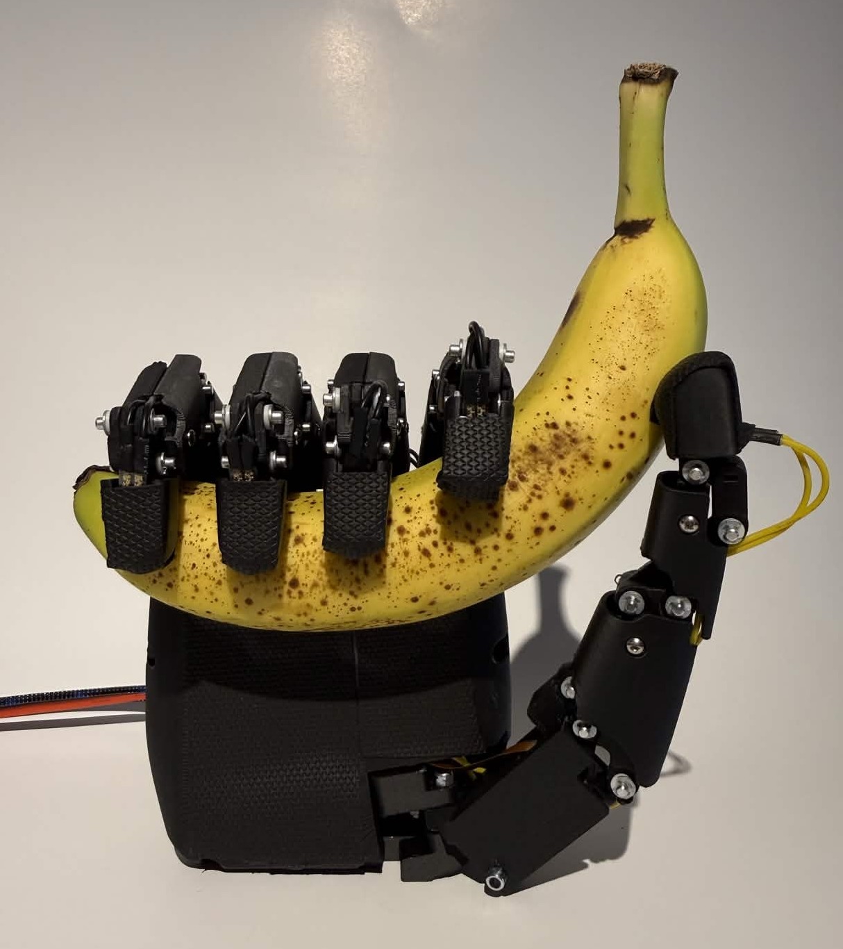
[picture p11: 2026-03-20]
assets/images/bh_holding_banana.jpg

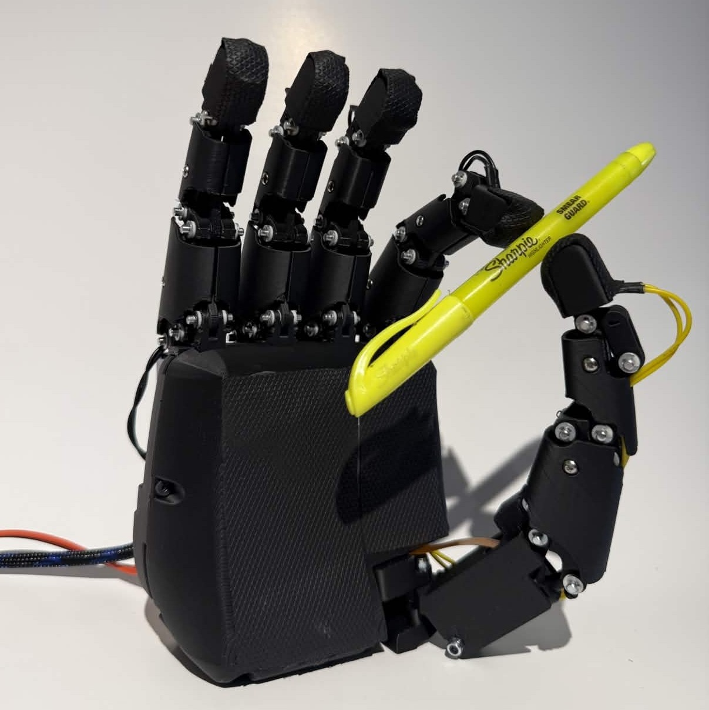
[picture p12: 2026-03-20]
assets/images/bh_holding_pen.jpg

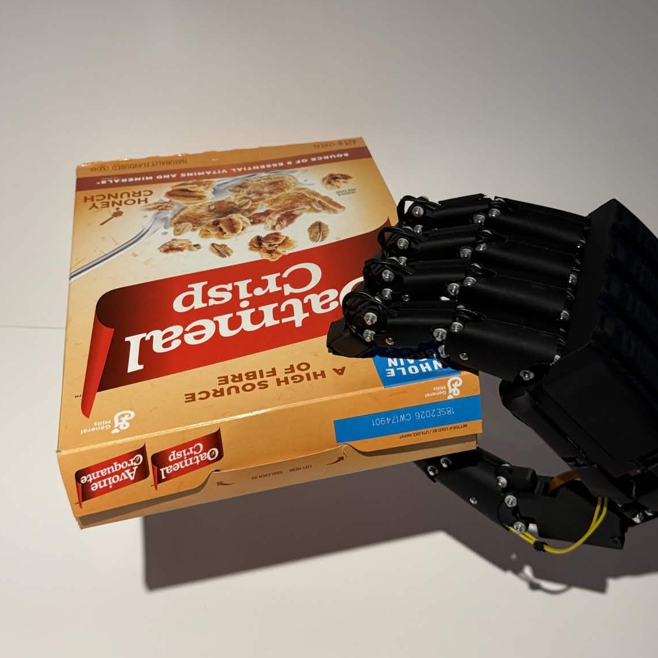
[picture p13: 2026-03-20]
assets/images/bh_holding_box.jpg

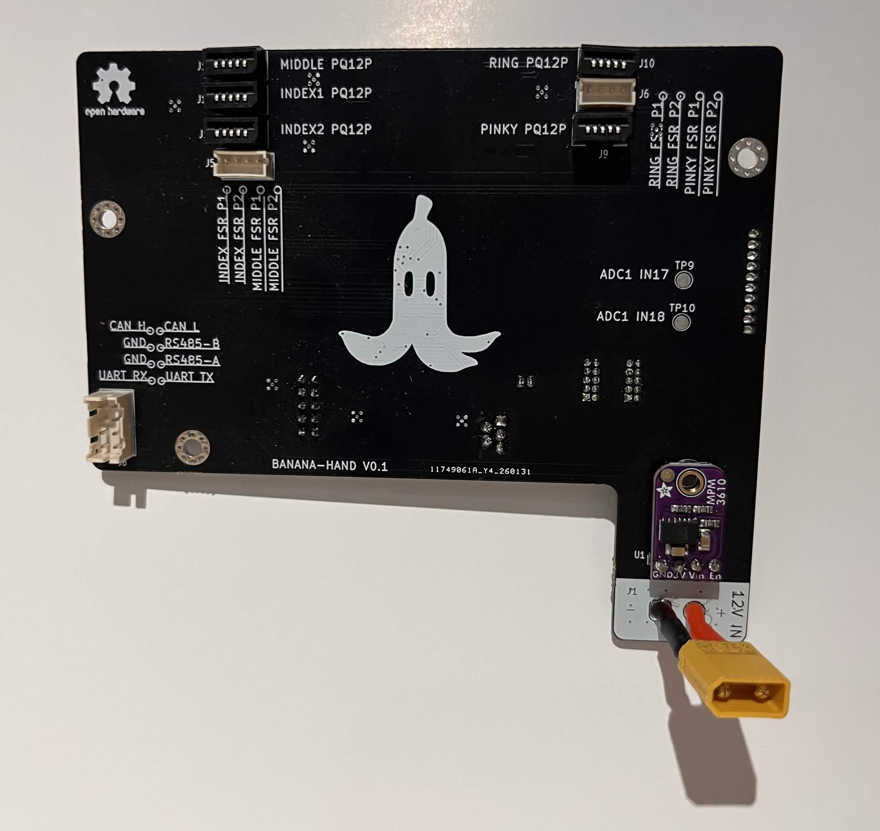
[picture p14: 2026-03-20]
assets/images/pcba_back.jpg

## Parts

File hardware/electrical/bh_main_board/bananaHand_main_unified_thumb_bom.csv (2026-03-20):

Reference | Qty | Value | DNP | Exclude from BOM | Exclude from Board | Footprint | Datasheet | MFR # | LCSC #
U6,U7,U8,U11,U12,U14,U15,U16 | 8 | DRV8876GTR |  |  |  | bananaHand:DRV8876GTR-MFG | https://www.ti.com/lit/ds/symlink/drv8876.pdf | DRV8876RGTR | C1852100
J18 | 1 | HLW5R-2C7LF |  |  |  | bananaHand:HLW5R-2C7LF |  | HLW5R-2C7LF | C5406452
J9,J10,J11,J12,J13 | 5 | HLW5S-2C7LF |  |  |  | bananaHand:HLW5S-2C7LF |  | HLW5S-2C7LF | C5406437
ART1 | 1 | ~ |  | Excluded from BOM |  | bananaHand:mk_banana_footprint
U1 | 1 | MPM3610_3V3_Buck_Brkout |  |  |  | bananaHand:MP3610_3V3_BUCK_BREAKOUT | https://github.com/adafruit/Adafruit-MPM3610-PCB
SW1,SW2 | 2 | SW_Push |  |  |  | Button_Switch_SMD:SW_SPST_TS-1088-xR025 | ~ | TS-1088R-02526 | C455281
C1,C2,C3,C6,C7,C8,C9,C12,C14,C15,C16,C18,C20,C22,C24,C26,C36,C38,C40,C42,C48,C50,C52,C54,C56,C58 | 26 | 100nF |  |  |  | Capacitor_SMD:C_0402_1005Metric | ~ | GRM155R71H104KE14D | C77020
C5 | 1 | 10nF |  |  |  | Capacitor_SMD:C_0402_1005Metric | ~ | GRM155R71H103KA88D | C77019
C13 | 1 | 4nF7 |  |  |  | Capacitor_SMD:C_0402_1005Metric | ~ | GRM1555C1H472JE01D | C1518204
C19,C23,C27,C39,C43,C51,C55,C59 | 8 | 22nF |  |  |  | Capacitor_SMD:C_0402_1005Metric | ~ | GRM155R71H223KA12D | C77023
C4,C11 | 2 | 4uF7 |  |  |  | Capacitor_SMD:C_0603_1608Metric_Pad1.08x0.95mm_HandSolder | ~ | GRM188R6YA475KE15D | C162274
C10 | 1 | 1uF |  |  |  | Capacitor_SMD:C_0603_1608Metric_Pad1.08x0.95mm_HandSolder | ~ | GCM188R71E105KA64D | C85862
C17,C21,C25,C37,C41,C57 | 6 | 47uF |  |  |  | Capacitor_SMD:CP_Elec_6.3x5.8 | ~ | EEEFP1V470AP | C401754
C49 | 1 | 100uF |  |  |  | Capacitor_SMD:CP_Elec_6.3x5.8 | ~ | EEEFT1V101AP | C128464
J1 | 1 | Conn_01x02_Pin |  |  |  | Connector_AMASS:AMASS_XT30UPB-M_1x02_P5.0mm_Vertical | ~ | XT30UPB-M | C428721
J20 | 1 | Conn_02x05_Odd_Even |  |  |  | Connector_JST:JST_PHD_B10B-PHDSS_2x05_P2.00mm_Vertical | ~ | B10B-PHDSS(LF)(SN) | C471519
J8 | 1 | Conn_02x04_Top_Bottom |  |  |  | Connector_JST:JST_PHD_B8B-PHDSS_2x04_P2.00mm_Vertical | ~ | B8B-PHDSS(LF)(SN) | C157975
J7 | 1 | Conn_01x10 |  |  |  | Connector_JST:JST_ZH_B10B-ZR_1x10_P1.50mm_Vertical | ~ | B10B-ZR(LF)(SN) | C158036
J4 | 1 | Conn_01x02_Pad |  |  |  | Connector_JST:JST_ZH_B2B-ZR_1x02_P1.50mm_Vertical | ~ | JST B2B-ZR(LF)(SN) | C158011
J5,J6 | 2 | Conn_01x04_Pin |  |  |  | Connector_JST:JST_ZH_B4B-ZR_1x04_P1.50mm_Vertical | ~ | JST B4B-ZR(LF)(SN) | C157997
J2,J3 | 2 | Conn_02x05_Top_Bottom |  |  |  | Connector_PinHeader_1.27mm:PinHeader_2x05_P1.27mm_Vertical | ~ | ZX-PZ1.27-2-5PZZ | C7501289
F2 | 1 | 750mA 36V |  |  |  | Fuse:Fuse_1206_3216Metric | https://www.lcsc.com/datasheet/C49196638.pdf | 1206L075/36NR | C49196638
F1 | 1 | 1A8 33V |  |  |  | Fuse:Fuse_1206_3216Metric_Pad1.42x1.75mm_HandSolder | https://www.lcsc.com/datasheet/C49318377.pdf | YTL 1206L100/33V | C49318377
D1,D2,D3,D4,D5 | 5 | LED |  |  |  | LED_SMD:LED_0402_1005Metric_Pad0.77x0.64mm_HandSolder | ~ | XL-1005UYC | C25503856
H1,H2,H3 | 3 | MountingHole |  | Excluded from BOM |  | MountingHole:MountingHole_2.5mm_Pad_Via | ~
U3 | 1 | STM32C071K8Tx |  |  |  | Package_QFP:LQFP-32_7x7mm_P0.8mm | https://www.st.com/resource/en/datasheet/stm32c071k8.pdf | STM32C071K8T6 | C43650208
U2 | 1 | STM32G474RETx |  |  |  | Package_QFP:LQFP-64_10x10mm_P0.5mm | https://www.st.com/resource/en/datasheet/stm32g474re.pdf | STM32G474RET6 | C521608
U4 | 1 | SN65HVD230DR |  |  |  | Package_SO:SOIC-8_3.9x4.9mm_P1.27mm | http://www.ti.com/lit/ds/symlink/sn65hvd230.pdf | SN65HVD230DR | C12084
U5 | 1 | SN65HVD1781 |  |  |  | Package_SO:SOIC-8_3.9x4.9mm_P1.27mm | https://www.ti.com/lit/ds/symlink/sn65hvd1781.pdf | SN65HVD1781DR | C42737
D7 | 1 | SM712_SOT23 |  |  |  | Package_TO_SOT_SMD:SOT-23 | https://www.littelfuse.com/~/media/electronics/datasheets/tvs_diode_arrays/littelfuse_tvs_diode_array_sm712_datasheet.pdf.pdf | SM712-02HTG | C172881
D6 | 1 | ESDCAN03-2BWY |  |  |  | Package_TO_SOT_SMD:SOT-323_SC-70 | https://www.st.com/en/protections-and-emi-filters/esdcan03-2bwy.html | ESDCAN03-2BWY | C1973833
R2,R4,R5,R11 | 4 | 100 |  |  |  | Resistor_SMD:R_0402_1005Metric_Pad0.72x0.64mm_HandSolder | ~ | ERJ2RKF1000X | C413063
R6,R7,R8,R9,R10,R12,R13,R14,R15,R16,R19,R22 | 12 | 10k |  |  |  | Resistor_SMD:R_0402_1005Metric_Pad0.72x0.64mm_HandSolder | ~ | RT0402BRD0710KL | C190095
R26,R29,R32,R41,R44,R50,R53,R56 | 8 | 11k |  |  |  | Resistor_SMD:R_0402_1005Metric_Pad0.72x0.64mm_HandSolder | ~ | RT0402BRE0711KL | C705643
R33,R34 | 2 | 3300 |  |  |  | Resistor_SMD:R_0402_1005Metric_Pad0.72x0.64mm_HandSolder | ~ | RC0402FR-073K3L | C137992
R1 | 1 | 100k | DNP |  |  | Resistor_SMD:R_0603_1608Metric_Pad0.98x0.95mm_HandSolder | ~ | RC0603FR-07100KL | C14675
R3 | 1 | 1200 |  |  |  | Resistor_SMD:R_0603_1608Metric_Pad0.98x0.95mm_HandSolder | ~ | RC0603FR-071K2L | C114605
R17,R18 | 2 | 60 |  |  |  | Resistor_SMD:R_0603_1608Metric_Pad0.98x0.95mm_HandSolder | ~ | 0603WAF604JT5E | C23090
R20,R23 | 2 | 10 |  |  |  | Resistor_SMD:R_0603_1608Metric_Pad0.98x0.95mm_HandSolder | ~ | RC0603FR-0710RL | C109318
R21 | 1 | 120 | DNP |  |  | Resistor_SMD:R_0603_1608Metric_Pad0.98x0.95mm_HandSolder | ~ | RC0603FR-07120RL | C114640
R24,R27,R30,R39,R42,R48,R51,R54 | 8 | 0 |  |  |  | Resistor_SMD:R_0603_1608Metric_Pad0.98x0.95mm_HandSolder | ~ | RC0603JR-070RL | C95177
R25,R28,R31,R40,R43,R49,R52,R55 | 8 | 0 | DNP |  |  | Resistor_SMD:R_0603_1608Metric_Pad0.98x0.95mm_HandSolder | ~ | RC0603JR-070RL | C95177
ART2 | 1 | Logo_Open_Hardware_Small |  | Excluded from BOM |  | Symbol:OSHW-Logo2_9.8x8mm_SilkScreen | ~
TP1,TP2,TP3,TP4,TP5,TP6,TP7,TP8,TP13,TP14,TP15,TP16,TP19,TP20,TP21,TP22,TP23,TP24 | 18 | TestPoint |  | Excluded from BOM |  | TestPoint:TestPoint_Pad_D1.0mm | ~
TP9,TP10 | 2 | TestPoint_Small |  | Excluded from BOM |  | TestPoint:TestPoint_Pad_D2.0mm | ~
TP11,TP12 | 2 | TestPoint_Small |  |  |  | TestPoint:TestPoint_Pad_D2.0mm | ~

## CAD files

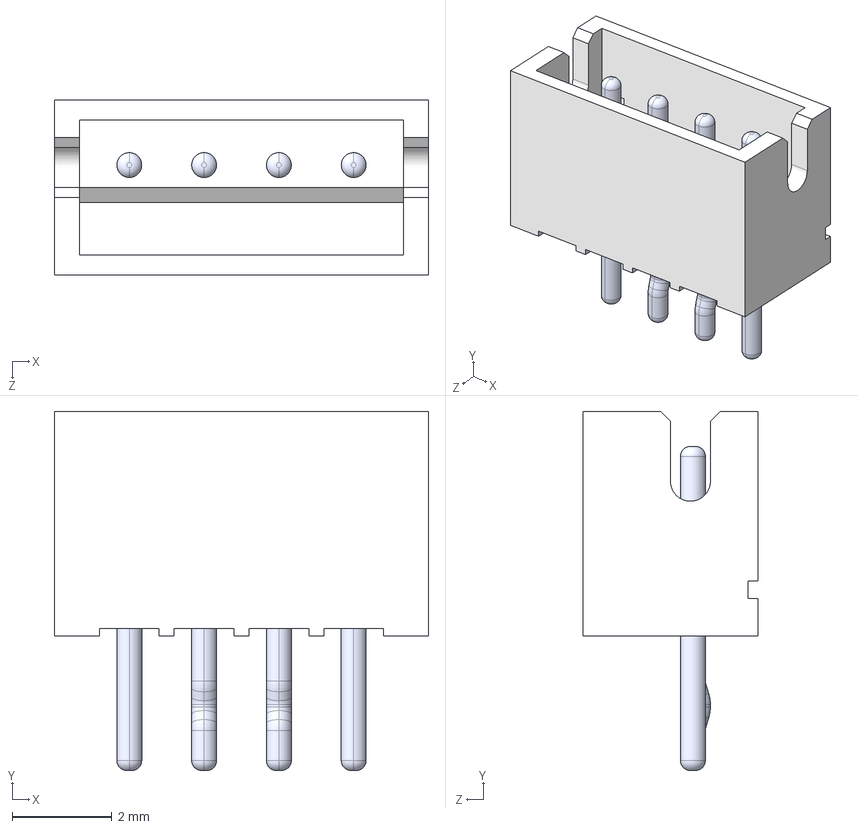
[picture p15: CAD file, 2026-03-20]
hardware/electrical/bh_main_board/3d_models/B4B-ZR.STEP
7.50 x 7.20 x 3.50 mm
BxB-ZR_4
pin_straight x 2
pin_Bent x 2

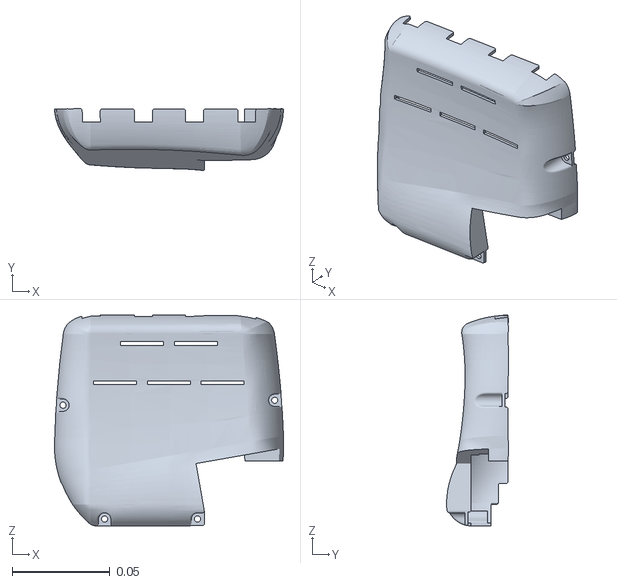
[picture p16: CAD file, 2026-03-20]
software/ros/src/banana_hand_visualization/mujoco/assets/palm_shell.stl
0.117 x 0.0317 x 0.108

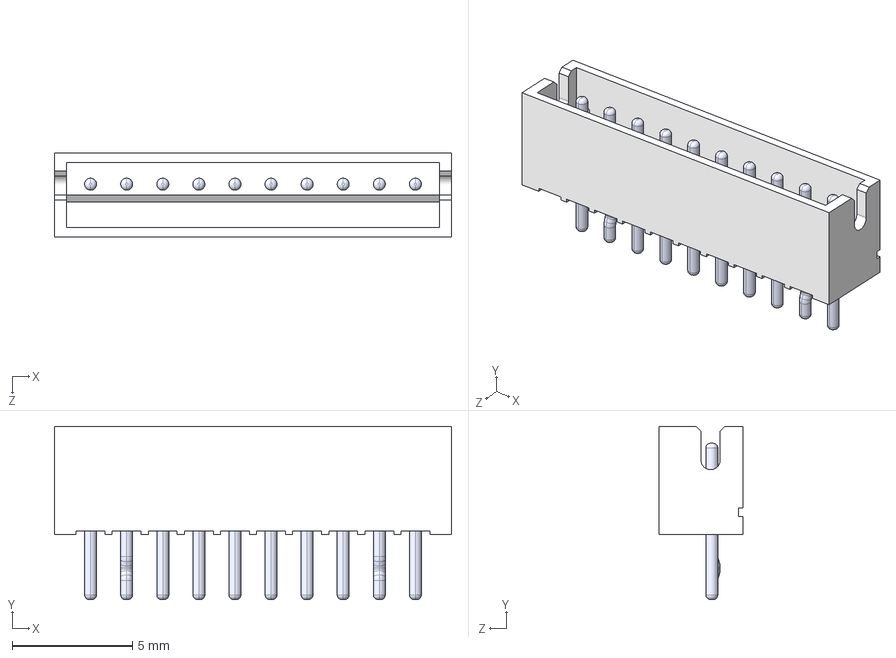
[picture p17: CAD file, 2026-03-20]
hardware/electrical/bh_main_board/3d_models/B10B-ZR.STEP
16.5 x 7.20 x 3.50 mm
BxB-ZR_10
pin_straight x 8
pin_Bent x 2

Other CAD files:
software/ros/src/banana_grasp_classification/resource/banana_scans/airpods_case/final_object_cloud_downsampled_ground_removed.ply
software/ros/src/banana_grasp_classification/resource/banana_scans/apple/final_object_cloud_downsampled.ply
software/ros/src/banana_grasp_classification/resource/banana_scans/cereal_box/final_object_cloud_downsampled_ground_removed.ply
software/ros/src/banana_grasp_classification/resource/banana_scans/cup/final_object_cloud_downsampled.ply
software/ros/src/banana_grasp_classification/resource/banana_scans/deodorant/final_object_cloud_downsampled_ground_removed.ply
software/ros/src/banana_grasp_classification/resource/banana_scans/egg/final_object_cloud.ply
software/ros/src/banana_grasp_classification/resource/banana_scans/eight_ball/final_object_cloud.ply
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

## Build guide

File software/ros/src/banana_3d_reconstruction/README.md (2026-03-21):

# banana_3d_reconstruction

Burst-mode RGB-D tabletop object scanning package for Intel RealSense depth cameras.

## What It Does

- Starts aligned RealSense color and depth streams with `pyrealsense2`.
- Shows a live OpenCV preview so you can always see the camera feed.
- Captures a short burst while the camera is held mostly still.
- Segments the tabletop object from the ROI-filtered frame on every burst frame when ROI selection is enabled, otherwise from the full frame.
- Fuses only the selected object-only clouds.
- Publishes the final clean cloud on `/object/point_cloud`.
- Publishes the saved scan directory on `/object_scan/completed_scan_dir` after each successful scan save.
- Saves the final cloud, downsampled cloud, one RGB image, metadata, and optional debug artifacts in a timestamped scan folder.

This package is intentionally optimized for one practical Demo 2 workflow:
- one object on a mostly clear desk
- camera held mostly still
- good diagonal viewing angle so the camera sees a few faces of the object
- clean partial object cloud for later geometric grip classification

## Recommended Workflow

1. Put one object on a mostly clear desk.
2. Hold the RealSense mostly still at a good diagonal angle.
3. Start the burst scan.
4. If needed, drag an ROI on the preview so only depth points inside that box are kept for the scan.
5. Let the node segment the tabletop object automatically from the ROI-filtered frame.
6. Use the saved partial point cloud for downstream geometry features or classification.

This is not trying to be a full 360 reconstruction system.

## Build

If you only want the scan node itself:

```bash
cd software/ros
source /opt/ros/humble/setup.bash
colcon build --symlink-install --packages-select banana_3d_reconstruction
source install/setup.bash
```

If you want the combined scan -> ground removal -> grasp-classification launch from `banana_grasp_classification`:

```bash
cd software/ros
source /opt/ros/humble/setup.bash
colcon build --symlink-install --packages-select \
  banana_interfaces banana_3d_reconstruction banana_grasp_classification
source install/setup.bash
```

## Runtime Dependencies

ROS 2 / Python packages used here include:
- `rclpy`
- `sensor_msgs`
- `sensor_msgs_py`
- `std_msgs`
- `std_srvs`
- `cv_bridge`
- `numpy`
- `opencv-python`
- `open3d`
- `pyrealsense2`

Important:
- `colcon build` in this workspace builds the ROS package, but it does not automatically install Python packages like `open3d` and `pyrealsense2`.
- Those may need manual installation on the machine before runtime.

## Run

```bash
cd software/ros
source /opt/ros/humble/setup.bash
source install/setup.bash
ros2 launch banana_3d_reconstruction object_scan.launch.py
```

Optional overrides:

```bash
ros2 launch banana_3d_reconstruction object_scan.launch.py \
  output_dir:=/tmp/banana_scans \
  show_preview:=true \
  enable_roi_selection:=true \
  device_serial:=<optional_camera_serial>
```

Optional service start:

```bash
ros2 service call /object_scan/start_scan std_srvs/srv/Trigger "{}"
```

End-to-end scan -> ground removal -> grasp classification:

```bash
ros2 launch banana_grasp_classification scan_to_grasp.launch.py
```

## Preview Controls

- `s`: start a burst scan
- `e`: end the current burst early
- `r`: reset the ROI to the full frame
- `q`: quit the node
- left mouse drag on the preview: set the ROI used for depth points during the next scan

The preview shows:
- the live color feed
- the active ROI rectangle when ROI selection is enabled

## Operator Instructions

1. Launch the node.
2. Place one object on a mostly clear tabletop.
3. Hold the RealSense mostly still at a good diagonal angle so it sees multiple faces of the object.
4. Press `s` or call `/object_scan/start_scan`.
5. Keep the camera still during the short burst.
6. Wait for processing to finish.
7. Check `final_object_cloud.ply` or subscribe to `/object/point_cloud`.

If you are running the combined scan-to-grasp launch, the saved scan directory is also published on `/object_scan/completed_scan_dir` so downstream grasp processing can start immediately.

## Automatic Object Selection

Each burst frame uses the same tabletop segmentation path:

1. Build the aligned RGB-D point cloud from the current ROI selection.
2. Fit the dominant plane from the ROI-filtered cloud.
3. Remove the desk plane.
4. Cluster the above-plane points.
5. Reject degenerate clusters such as tiny slivers, line-like fragments, and sparse junk.
6. Prefer the remaining clusters that are:
   - larger
   - closer to the image center
   - more object-like in 3D extent

This assumes there is one main tabletop object and minimal clutter.

When `enable_roi_selection:=true` (the default), the preview starts with a full-frame ROI so behavior stays unchanged until you drag a smaller box.

## Burst Fusion

- The node assumes very small camera motion.
- It fuses only the selected object clouds, never the full raw scene.
- It tries conservative ICP first.
- If ICP is not good enough but the selected cluster centroid barely moved, it falls back to identity accumulation.
- If a frame looks bad, it is skipped.

## Final Cleanup

After burst fusion, the node runs aggressive cleanup:

1. One more dominant-plane removal on the fused cloud when possible.
2. Keep only points above that plane.
3. Voxel downsample.
4. Statistical outlier removal.
5. Radius outlier removal.
6. Largest-cluster extraction.
7. Normal estimation.

This is specifically meant to remove leftover desk patches and small junk before saving the final cloud.

## Topics

- `/object/point_cloud` (`sensor_msgs/msg/PointCloud2`): final cleaned object cloud
- `/object_scan/completed_scan_dir` (`std_msgs/msg/String`): absolute path to the newly saved scan directory
- `/object_scan/status` (`std_msgs/msg/String`): scan state updates
- `/object_scan/debug/raw_frame_cloud` (`sensor_msgs/msg/PointCloud2`, optional)
- `/object_scan/debug/plane_removed_cloud` (`sensor_msgs/msg/PointCloud2`, optional)
- `/object_scan/debug/selected_object_cloud` (`sensor_msgs/msg/PointCloud2`, optional)

## Services

- `/object_scan/start_scan` (`std_srvs/srv/Trigger`)
- `/object_scan/save_last_scan` (`std_srvs/srv/Trigger`)

## Saved Outputs

- `scan_YYYYMMDD_HHMMSS/final_object_cloud.ply`
- `scan_YYYYMMDD_HHMMSS/final_object_cloud_downsampled.ply`
- `scan_YYYYMMDD_HHMMSS/final_rgb_image.png`
- `scan_YYYYMMDD_HHMMSS/metadata.json`

When `save_intermediate_debug_clouds:=true`, the package also saves:
- raw cloud per keyframe
- plane-removed cloud per keyframe
- selected object cloud per keyframe
- registered selected cloud per accepted keyframe
- `fused_segmented_cloud_pre_cleanup.ply`
- `final_cleaned_object_cloud.ply`
- one debug JSON per frame with candidate cluster stats, degeneracy checks, selection reason, and accept/reject status

## Limitations

- This produces a practical partial tabletop object cloud, not a guaranteed watertight 360 reconstruction.
- The underside of an object resting on a desk is not observable in a normal tabletop scan.
- It assumes one main object on a mostly clear desk.
- Large camera motion during the burst will reduce quality because the node is intentionally tuned for mostly-still capture, not handheld reconstruction.

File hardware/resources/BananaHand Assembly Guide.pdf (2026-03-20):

# Assembly Guide

# Parts List

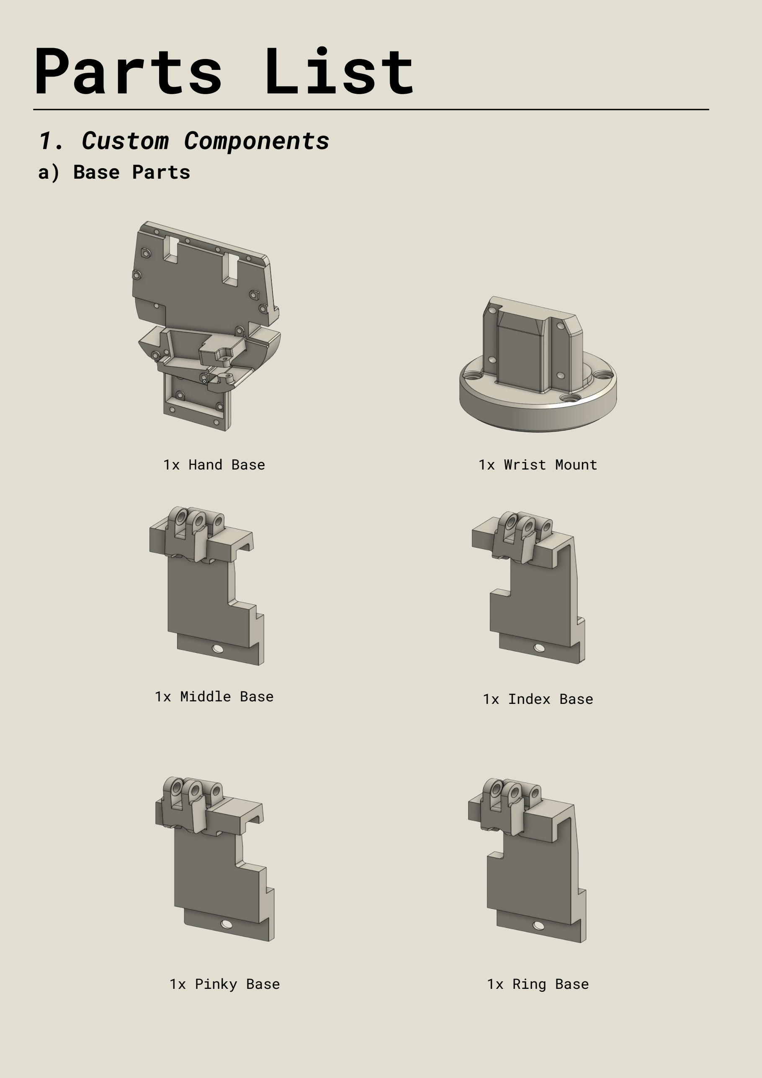
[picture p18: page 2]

### 1. Custom Components

1x Hand Base

a) Base Parts
1x Pinky Base | 1x Ring Base
1x Middle Base | 1x Index Base

1x Wrist Mount

### 1. Custom Components

4x MCP-1

b) Finger Parts

4x DIP-1

4x PIP-1 | 4x PIP-2

4x MCP-2

# Parts List

### 1. Custom Components

1x Clevis

c) Thumb Parts
1x Thumb Base | 1x TM-1

1x Clevis Link

1x TM-2 | 1x PIPT-1
1x PIPT-2 | 1x DIPT-1

# Parts List

### 1. Custom Components

1x Palm Shell | 5x Fingertip
d) Shell Parts

4x PIP-SHELL-A

1x Back Shell

4x PIP-SHELL-B | 5x MCP-SHELL-A
5x MCP-SHELL-B | 1x PIPT-SHELL-A | 1x PIPT-SHELL-B
1x TM-SHELL-A | 1x TM-SHELL-A

# Parts List

### 2. Electronic Components

1x ACTUONIX PQ-12 63:1 Linear Actuator

a) Actuators and PCB

5x ACTUONIX PQ-12 30:1 Linear Actuator

1x Custom PCB

# Parts List

80x 3mm Shaft OD E-Clips

20x M3x10mm Clevis Pin

### 3. OTS Mechanical Components

a) Fasteners, Pins, Bushings and More
20x M3x6mm Socket Head | 3x M3x12mm Socket Head | 5x M3x14mm Socket Head
2x M3x20mm Socket Head | 9x M3 Nylon Lock Nut | 27x M2.5x5mm Self-Tap
4x M4x20mm Socket Head | 4x M4 Nylon Lock Nut | 16x M3x4mm Heat Set Insert
5x M3x6mm Heat Set Insert | 20x M3x16mm Clevis Pin
80x 3mm Shaft Bushing | 80x M3 PTFE Washer

# Parts List

# Finger Assembly

# Finger Assembly

### 1. Attach PQ12 30:1 Actuator to Index Base

using M3x14mm Socket Head + M3 Lock Nut

# Finger Assembly

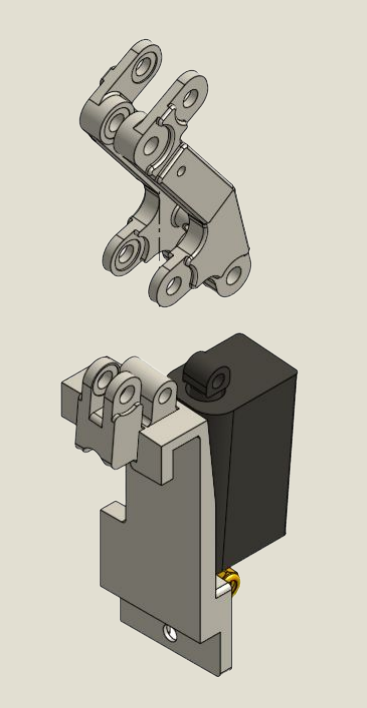
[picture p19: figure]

### 2. Attach MCP-1 to PQ-12 Actuator using 16mm

Clevis Pin, E-Clip, Bushing, and Washer

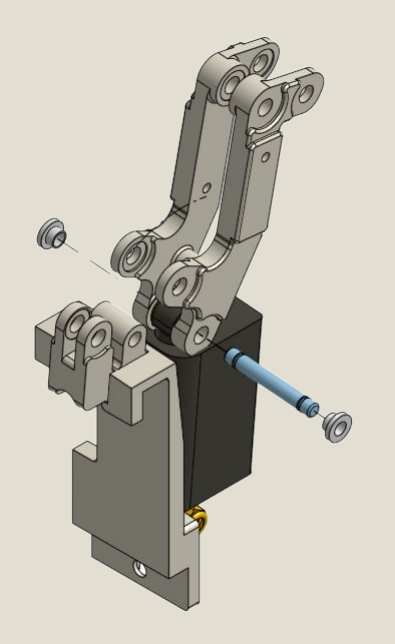
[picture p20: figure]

# Finger Assembly

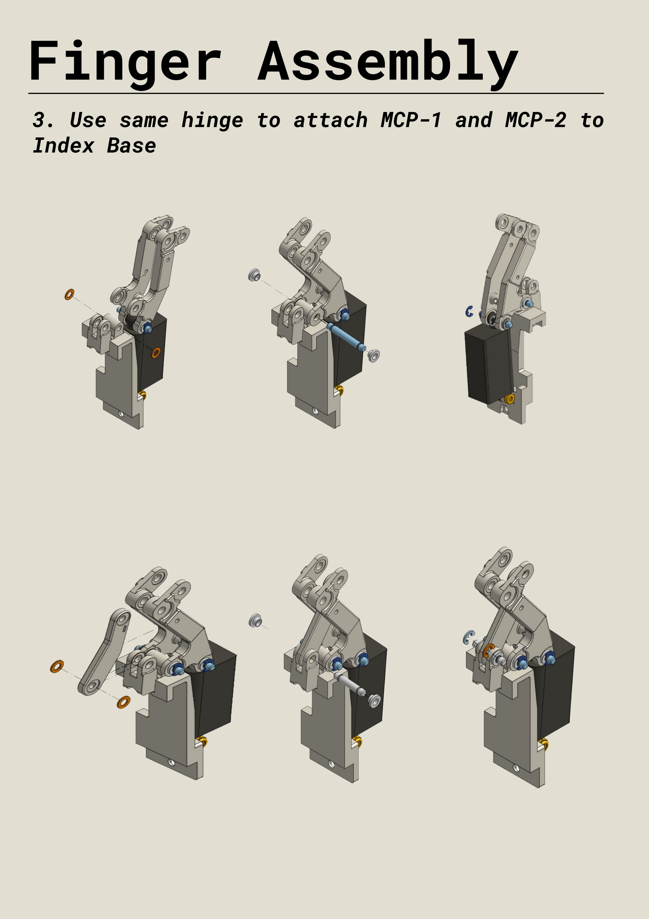
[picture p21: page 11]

### 3. Use same hinge to attach MCP-1 and MCP-2 to

Index Base

### 4. Attach PIP-1 to MCP-1 and MCP-2

# Finger Assembly

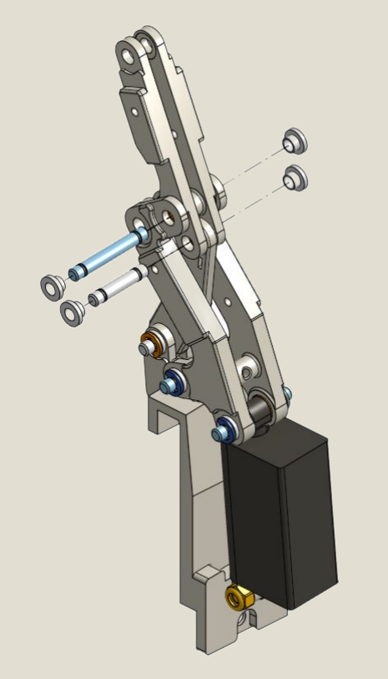
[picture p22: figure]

### 5. Attach PIP-2 to MCP-1

# Finger Assembly

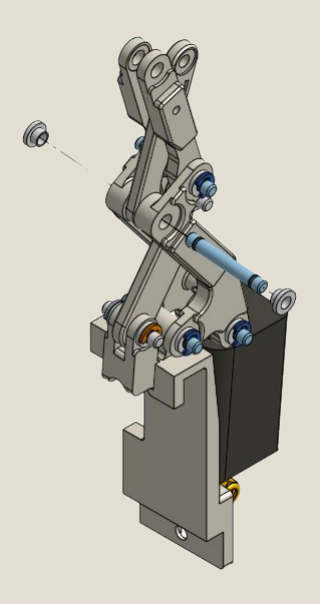
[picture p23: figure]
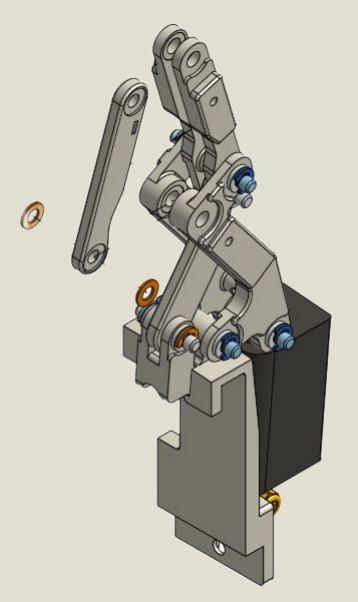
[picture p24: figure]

### 6. Attach DIP to PIP-1 and PIP-2

# Finger Assembly

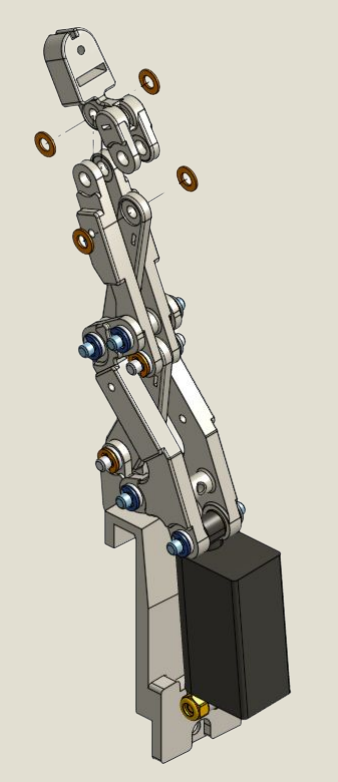
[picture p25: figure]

### 7. Attach Fingertip to DIP-1 using M2.5

Self-Tap

# Finger Assembly

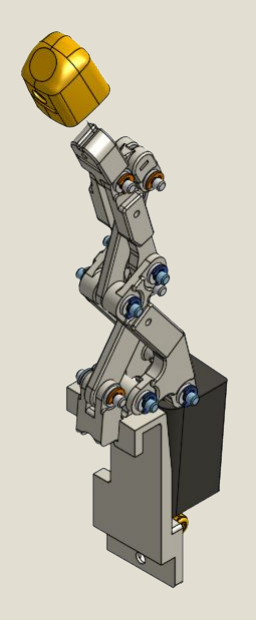
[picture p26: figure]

### 8. Attach PIP and MCP Shells

# Finger Assembly

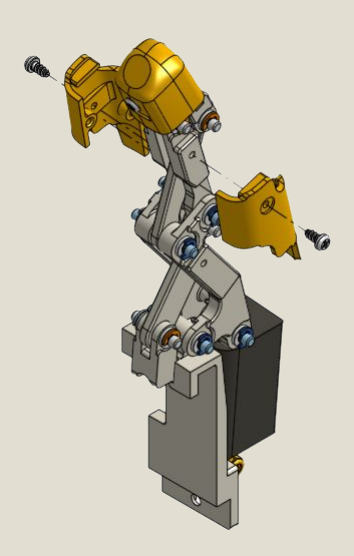
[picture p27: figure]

### 9. Completed Finger Assembly, repeat steps for

Middle, Ring, and Pinky fingers

# Finger Assembly

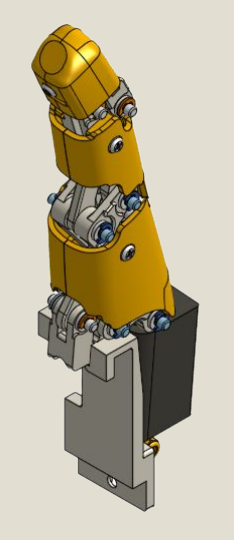
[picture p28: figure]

# Thumb Assembly

# Thumb Assembly

### 1. Attach Clevis to PQ-12 63:1 Actuator Piston

using M3x14mm Socket Head and M3 Lock Nut

# Thumb Assembly

### 2. Attach Clevis Link to Clevis using M3x12mm

Socket Head and M3 Lock Nut

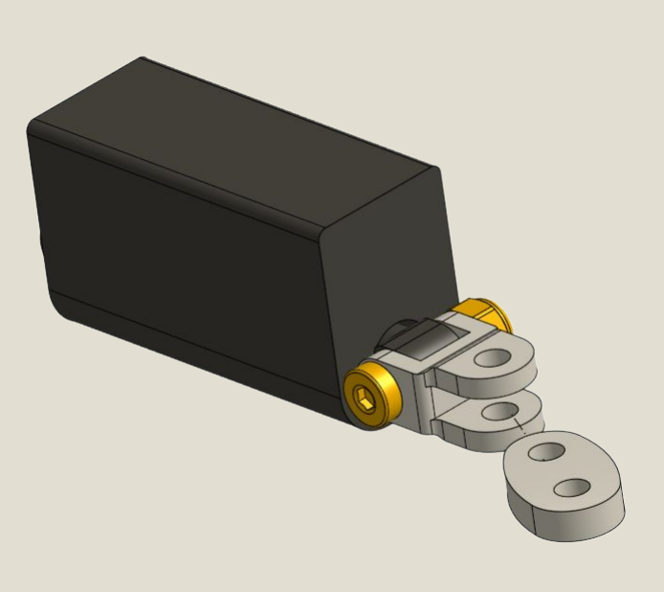
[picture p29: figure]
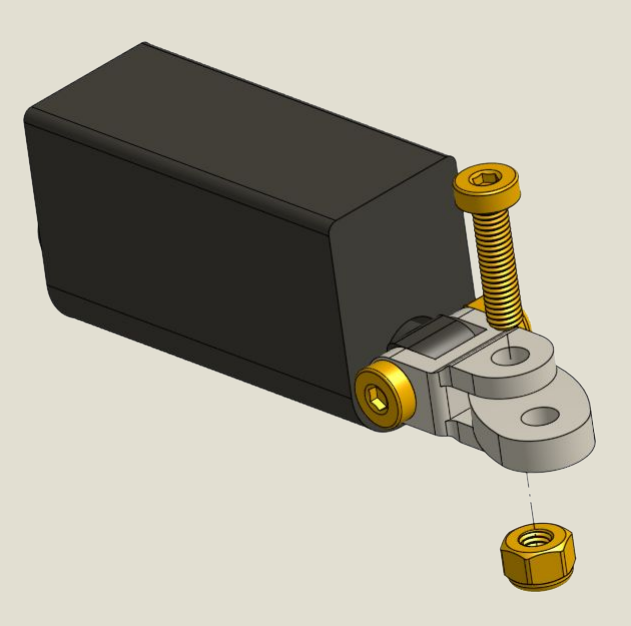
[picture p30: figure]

# Thumb Assembly

### 3. Attach Thumb Base using M3x12mm Socket Head

and M3 Lock Nut

# Thumb Assembly

### 4. Attach PQ-12 30:1 Actuator to Thumb Base

using M3x20mm Socket Head and M3 Lock Nut

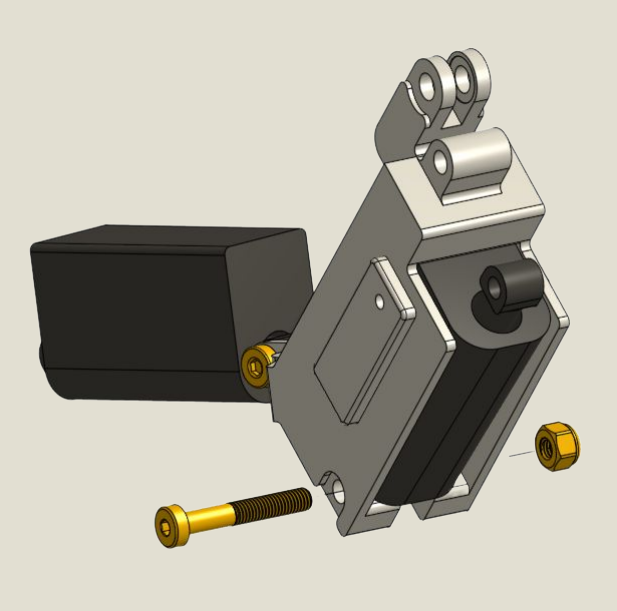
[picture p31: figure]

# Thumb Assembly

### 5. Attach Thumb Linkage Mechanism to Thumb

Base using same strategy as shown in Finger Assembly Steps 2-9

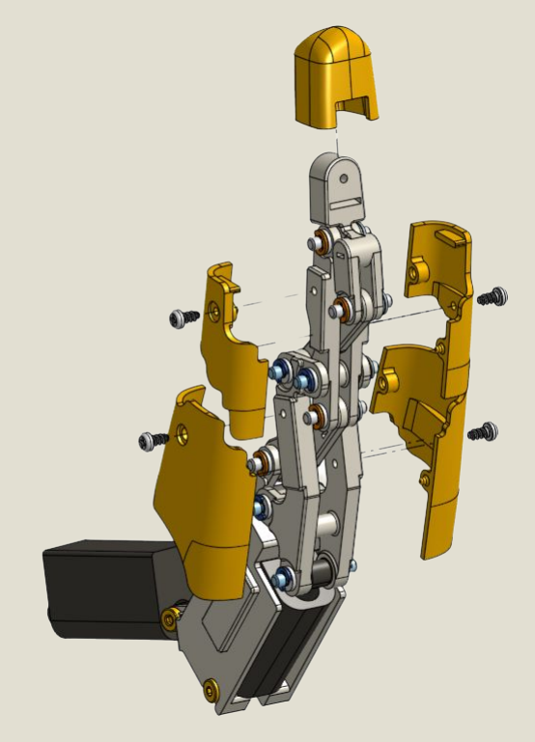
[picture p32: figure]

# Thumb Assembly

### 5. Attach TM-SHELL to Thumb Base

# Thumb Assembly

### 6. Completed Thumb Assembly

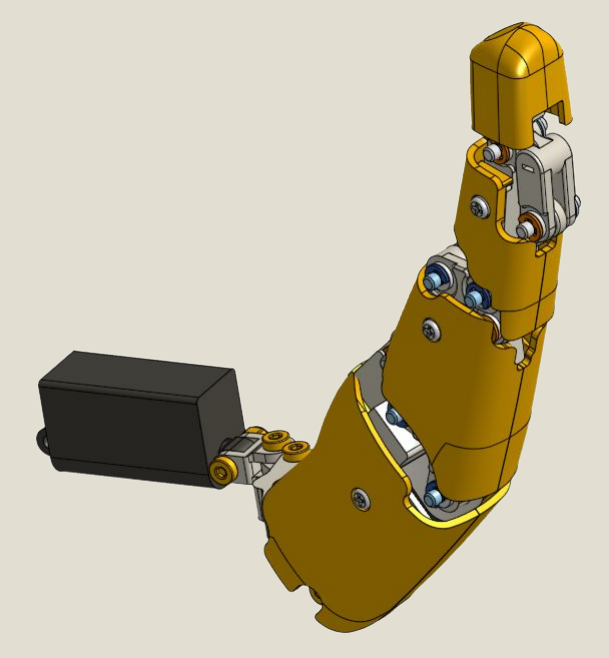
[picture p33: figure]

# Main Assembly

### 1. Add 4mm M3 Heat Set Inserts to Hand Base

# Main Assembly

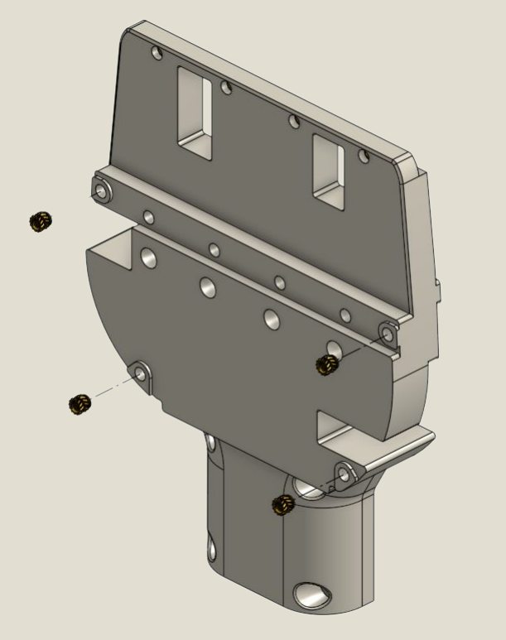
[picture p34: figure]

### 2. Add 6mm M3 Heat Set Inserts to Hand Base

# Main Assembly

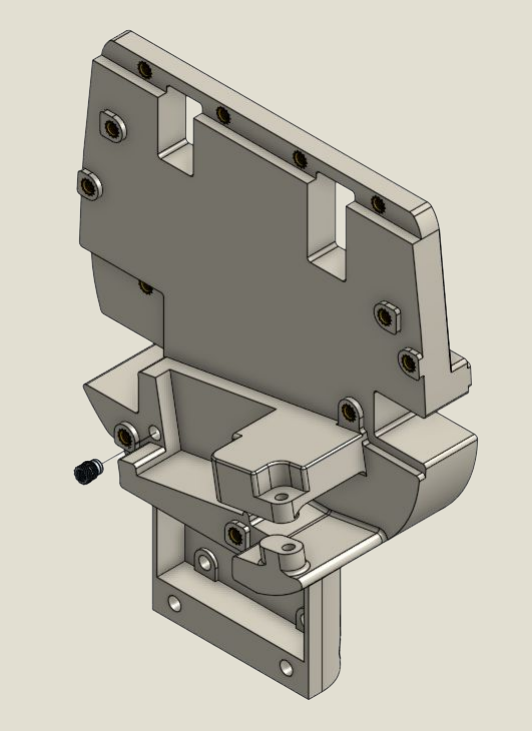
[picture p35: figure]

### 3. Attach Finger Assemblies to Main Base using

M3x6mm Socket Head

# Main Assembly

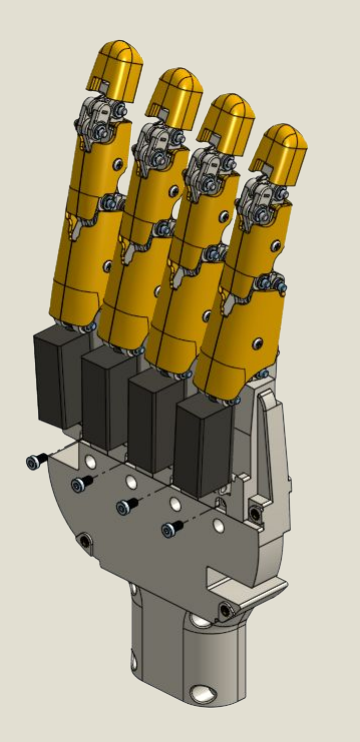
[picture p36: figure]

### 4. Attach Thumb Assembly to Main Base using

M3x12mm and M3x20mm Socket Head with M3 Lock Nut

# Main Assembly

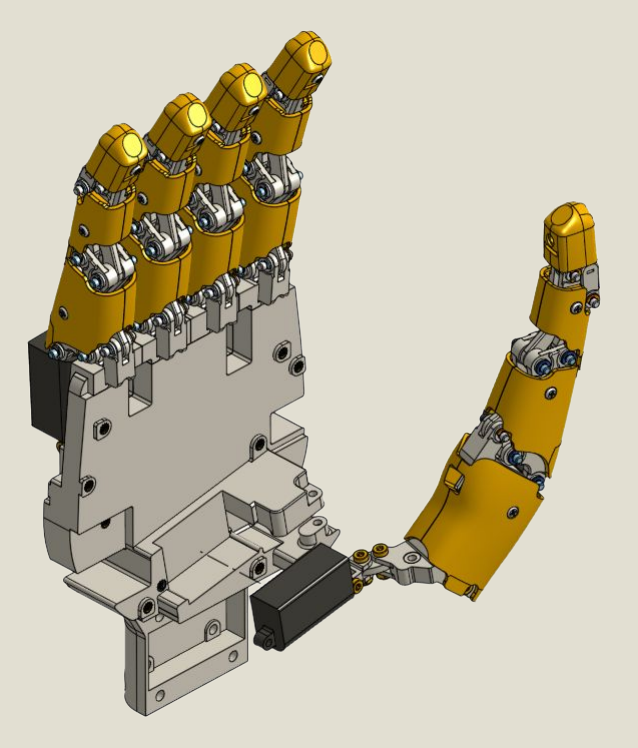
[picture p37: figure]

### 5. Attach PCB to Hand Base using M3x6mm Socket

Head

# Main Assembly

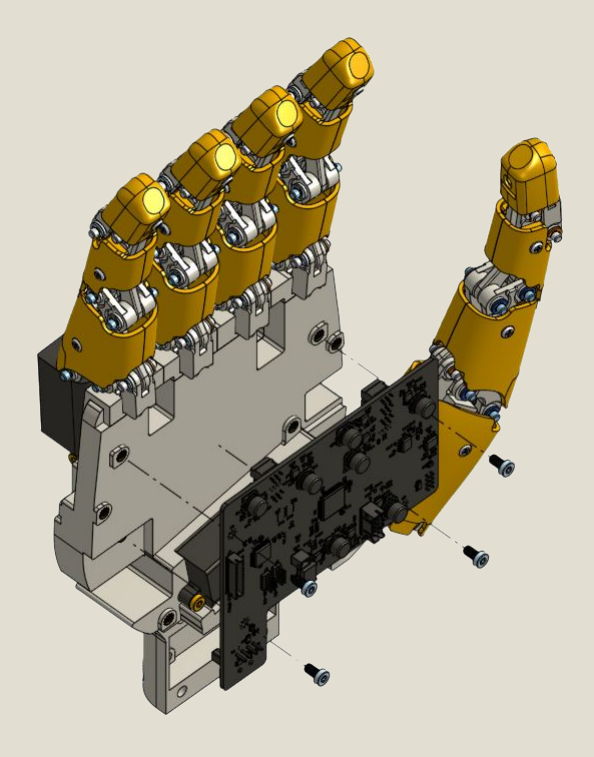
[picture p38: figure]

### 6. Attach Back Shell and Palm Shell to Hand

Base using M3x6mm Socket Head

# Main Assembly

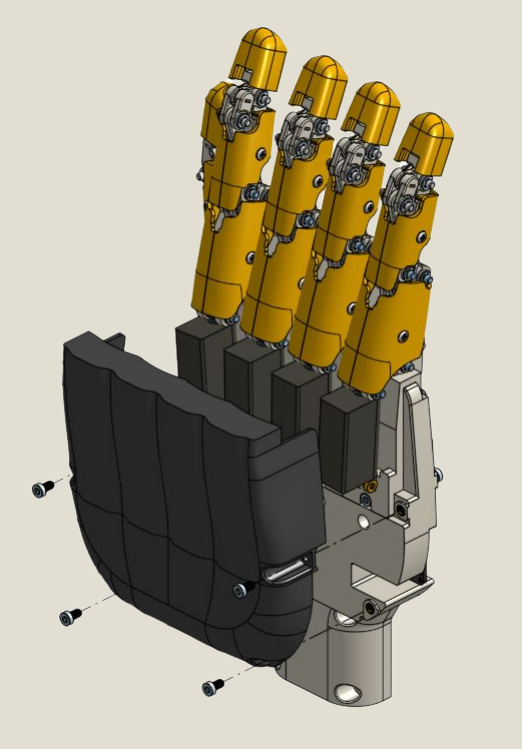
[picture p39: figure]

### 7. Attach Wrist Mount to Hand Base using

M4x20mm Socket Head and M4 Lock Nuts

# Main Assembly

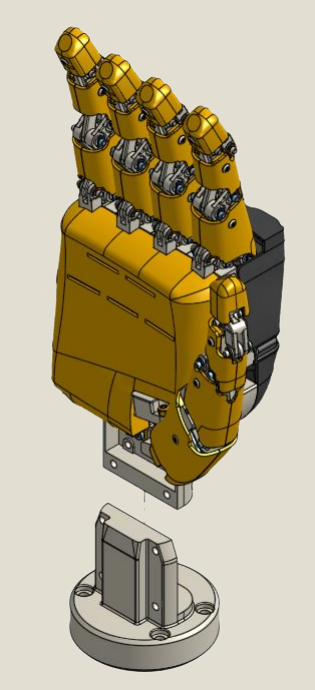
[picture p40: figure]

### 8. Complete BananaHand Assembly

# Main Assembly

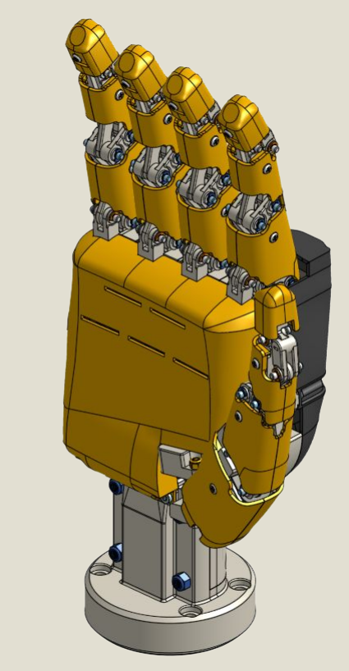
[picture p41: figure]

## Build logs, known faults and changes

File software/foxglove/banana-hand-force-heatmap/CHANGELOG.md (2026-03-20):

# Changelog

## 0.0.1
- Initial Banana Hand force heatmap panel scaffold
- Added support for `/banana_hand/force_state`
- Added fallback parsing for raw `/rx_force` array-style messages

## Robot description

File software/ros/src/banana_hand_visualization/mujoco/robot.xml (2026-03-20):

<?xml version="1.0" ?>
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
<mujoco model="newbanana">
  <compiler angle="radian" meshdir="assets" autolimits="true"/>
  <default>
    <default class="newbanana">
      <joint damping="0.0005"/>
      <position kp="2000" dampratio="0.0001"/>
      <default class="visual">
        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
      </default>
      <default class="collision">
        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
      </default>
    </default>
  </default>
  <worldbody>
    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
    <body name="wrist_mount" pos="0 0 0" quat="1 0 0 0" childclass="newbanana">
      <inertial pos="-4.88573e-06 -0.00187167 0.0129427" mass="0.131729" fullinertia="7.23325e-05 7.07738e-05 7.75665e-05 -3.408e-09 3.0974e-08 7.13635e-06"/>
      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
      <body name="hand_base" pos="-0.01886 -0.003 0.05977" quat="0.707107 0.707107 -0 0">
        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
        <inertial pos="0.0227711 0.0368198 -0.00970441" mass="0.24691" fullinertia="0.00031481 0.000210808 0.000492602 4.41066e-06 -8.72699e-06 6.42656e-06"/>
        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
        <body name="index_base" pos="0.0607318 0.108855 -0.008" quat="0 -1 0 -0">
          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
          <inertial pos="-0.000915189 0.0173428 0.00659471" mass="0.00908632" fullinertia="3.91326e-06 7.16004e-07 3.97477e-06 9.919e-08 2.4255e-08 -8.53174e-07"/>
          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
          <body name="actuator_housing" pos="-0.000613381 0.0375721 0.0185" quat="0.706541 -0.030325 0.706456 0.0282795">
            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
            <joint axis="0 0 1" name="indexrev1" type="hinge"/>
            <inertial pos="-0.00615503 -0.0206966 -0.0025" mass="0.012849" fullinertia="1.75829e-06 7.16933e-07 1.97489e-06 -4.3769e-08 0 0"/>
            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
            <body name="actuator_piston" pos="-0 -0.00975 -0.0025" quat="0 0 0.707107 0.707107">
              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
              <joint axis="0 0 1" name="indexpiston" type="slide" range="-0.018249999999999232 7.686993402922226e-16"/>
              <inertial pos="0 0 -0.0184461" mass="0.00107731" fullinertia="1.20116e-07 1.20153e-07 4.363e-09 0 -0 -0"/>
              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
              <body name="mcp_1" pos="0 -0.00314 -0.0341" quat="0.696301 -0.696301 0.123148 0.123148">
                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
                <joint axis="0 0 1" name="indexrev2" type="hinge"/>
                <inertial pos="-0.00399802 0.0250212 0.00314" mass="0.00631644" fullinertia="1.7563e-06 3.51669e-07 1.67536e-06 1.96427e-07 -6.34e-10 1.61e-09"/>
                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
                <body name="pip_2" pos="-0.0106252 0.047153 0.00464" quat="0.973728 0 -0 -0.227713">
                  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
                  <joint axis="0 0 1" name="indexrev5" type="hinge"/>
                  <inertial pos="-0.000165532 0.0185904 -0.0015" mass="0.00109766" fullinertia="1.49177e-07 6.342e-09 1.54003e-07 -1.509e-09 0 -0"/>
                  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
                  <body name="dip_1" pos="-0 0.0365 0.0001" quat="0 0.918852 0.394602 -0">
                    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
                    <joint axis="0 0 1" name="indexrev8" type="hinge" range="-1.283124704645382 0.08370581700095858"/>
                    <inertial pos="-0.00485498 -0.0149142 0.0016" mass="0.00216187" fullinertia="1.75757e-07 5.3677e-08 1.95113e-07 -5.3219e-08 0 -0"/>
                    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
                    <body name="fingertip" pos="-0.01125 -0.025 0.0016" quat="0 -0.707107 0 -0.707107">
                      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
                      <inertial pos="-1.53291e-05 8.9755e-06 0.00556374" mass="0.00195277" fullinertia="1.25657e-07 1.08494e-07 1.27514e-07 1.8e-10 -4.5e-11 -8.679e-09"/>
                      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
                    </body>
                  </body>
                </body>
                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
                <body name="mcp_shell_a" pos="-0.00183227 0.0248419 -0.00561" quat="1 0 -0 0">
                  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
                  <inertial pos="-0.00210081 0.000899501 0.000749709" mass="0.00287674" fullinertia="3.67204e-07 2.59935e-07 5.58987e-07 1.04558e-07 -1.31e-08 9.211e-09"/>
                  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
                </body>
                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
                <body name="mcp_shell_b" pos="-0.00700145 0.0379582 0.01189" quat="0 1 0 0">
                  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
                  <inertial pos="0.00319467 0.011403 0.000809275" mass="0.00278046" fullinertia="3.86254e-07 2.55766e-07 5.74541e-07 -1.08115e-07 -9.775e-09 -1.0119e-08"/>
                  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
                </body>
              </body>
            </body>
          </body>
          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
          <body name="mcp_2" pos="-0.000183516 -0.0159056 -0.006" quat="0.677803 -0.144632 -0.692157 0.201452">
            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
            <joint axis="0 0 1" name="indexrev4" type="hinge"/>
            <inertial pos="-0.0010236 -0.0147621 -0.0015" mass="0.00124532" fullinertia="1.43754e-07 1.3387e-08 1.55402e-07 -1.8082e-08 -0 -0"/>
            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
            <body name="pip_1" pos="-0.005 -0.0325 -0.0031" quat="0.883363 0 0 -0.46869">
              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
              <joint axis="0 0 1" name="indexrev6" type="hinge" range="-0.9878811485522565 0.10779664540577816"/>
              <inertial pos="0.000159546 -0.0240179 0.0016" mass="0.00293121" fullinertia="5.03928e-07 5.484e-08 4.75801e-07 -2.839e-09 0 7.37e-10"/>
              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
              <body name="pip_shell_a" pos="0 -0.0234 0.0082" quat="0 -1 0 0">
                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
                <inertial pos="0.000950206 0.000347234 0.000969168" mass="0.00156225" fullinertia="1.5107e-07 6.8794e-08 1.95961e-07 4.9385e-08 -1.725e-09 8.462e-09"/>
                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
              </body>
              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
              <body name="pip_shell_b" pos="-0 -0.03255 -0.005" quat="1 -0 -0 -0">
                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
                <inertial pos="0.000862039 0.00821021 0.000964796" mass="0.00156476" fullinertia="1.58144e-07 6.8853e-08 2.03054e-07 -5.0112e-08 -7.65e-10 -8.669e-09"/>
                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
              </body>
            </body>
          </body>
        </body>
        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
        <body name="middle_base" pos="0.0343032 0.108855 -0.008" quat="0 -1 0 -0">
          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
          <inertial pos="-0.00110743 0.0165611 0.00645915" mass="0.00951968" fullinertia="4.19962e-06 7.54185e-07 4.25616e-06 -1.1399e-08 1.5511e-08 -9.14817e-07"/>
          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
          <body name="actuator_housing_2" pos="0.0018604 0.0366644 0.0185" quat="0.707088 -0.00719421 0.70707 0.00514696">
            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
            <joint axis="0 0 1" name="middlerev1" type="hinge"/>
            <inertial pos="-0.00615503 -0.0206966 -0.0025" mass="0.012849" fullinertia="1.75829e-06 7.16933e-07 1.97489e-06 -4.3769e-08 0 -0"/>
            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
            <body name="actuator_piston_2" pos="-0 -0.00975 -0.0025" quat="0 0 -0.707107 -0.707107">
              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
              <joint axis="0 0 1" name="middlepiston" type="slide" range="-0.018249999999999877 1.222980050563649e-16"/>
              <inertial pos="0 -0 -0.0184461" mass="0.00107731" fullinertia="1.20116e-07 1.20153e-07 4.363e-09 0 -0 -0"/>
              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
              <body name="mcp_1_2" pos="0 0.0036 -0.0341" quat="0.696301 0.696301 0.123148 -0.123148">
                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
                <joint axis="0 0 1" name="middlerev2" type="hinge"/>
                <inertial pos="-0.00399802 -0.0250212 0.0036" mass="0.00631644" fullinertia="1.7563e-06 3.51669e-07 1.67536e-06 -1.96427e-07 6.34e-10 1.61e-09"/>
                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
                <body name="pip_2_2" pos="-0.0106252 -0.047153 0.0021" quat="0 -0.973728 -0.227713 0">
                  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
                  <joint axis="0 0 1" name="middlerev5" type="hinge"/>
                  <inertial pos="-0.000165532 0.0185904 -0.0015" mass="0.00109766" fullinertia="1.49177e-07 6.342e-09 1.54003e-07 -1.509e-09 -0 0"/>
                  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
                  <body name="dip_1_2" pos="-0 0.0365 0.0001" quat="0 -0.918852 -0.394602 -0">
                    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
                    <joint axis="0 0 1" name="middlerev8" type="hinge" range="-1.2831247046433738 0.08370581700296675"/>
                    <inertial pos="-0.00485498 -0.0149142 0.0016" mass="0.00216187" fullinertia="1.75757e-07 5.3677e-08 1.95113e-07 -5.3219e-08 0 -0"/>
                    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
                    <body name="fingertip_2" pos="-0.01125 -0.025 0.0016" quat="0 0.707107 -0 0.707107">
                      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

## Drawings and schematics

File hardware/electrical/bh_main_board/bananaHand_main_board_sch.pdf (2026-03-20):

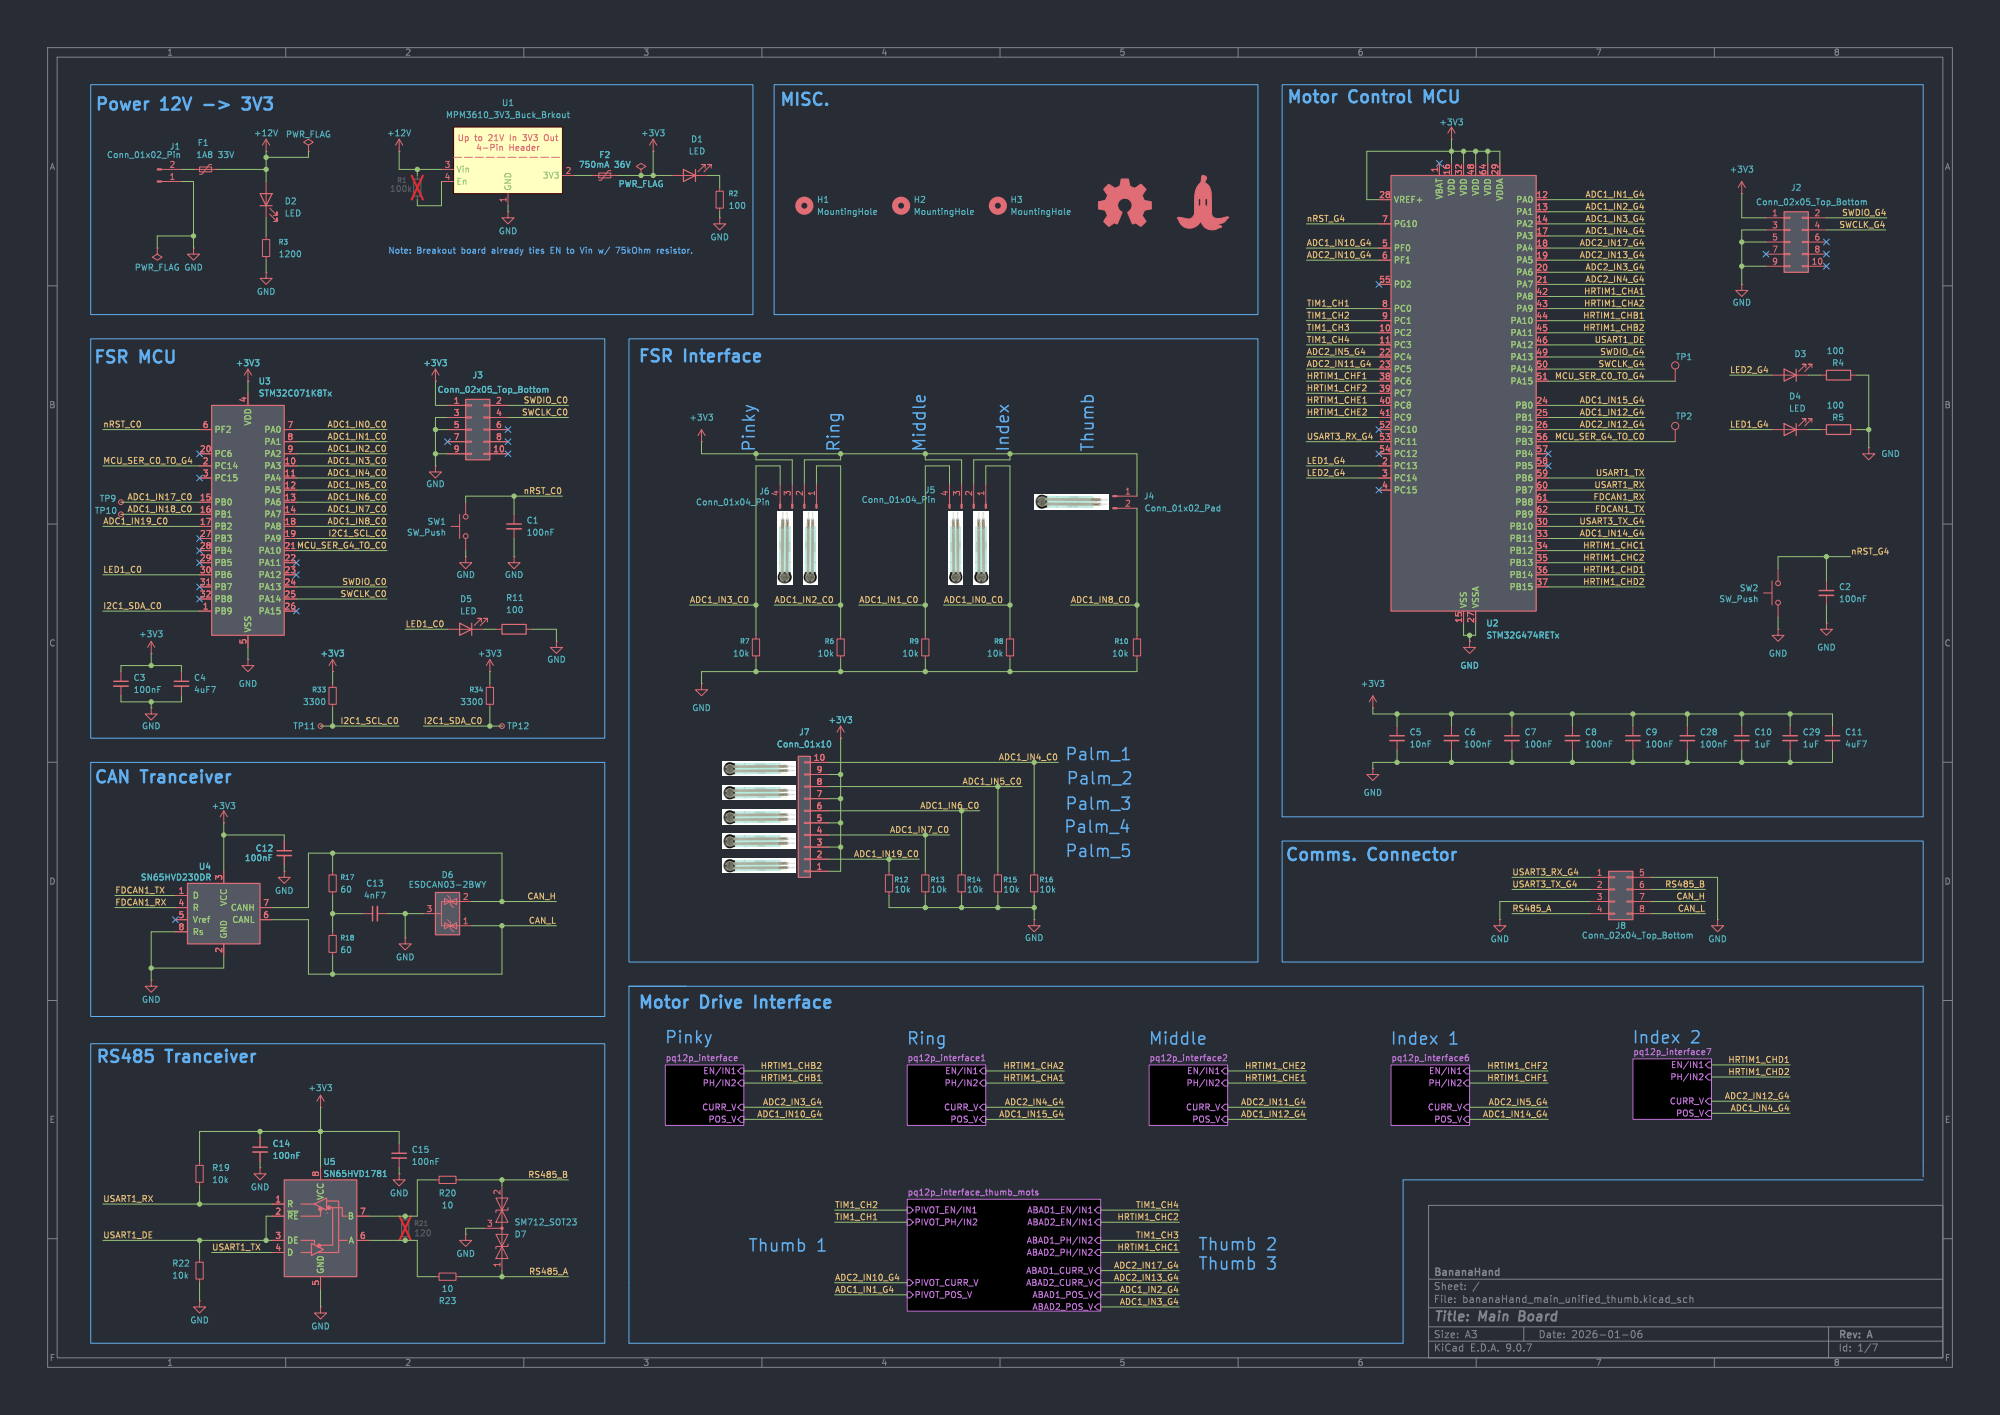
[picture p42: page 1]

Up to 21V In 3V3 Out

1 VDD 16 VDD 32 VSS 15 VDD 48 VSSA 27 VDD 64 VDDA 29 PA0 12 PA1 13 PA2 14 PA3 17 PA4 18 PA5 19 PA6 20 PA7 21 PA8 42 PA9 43 PA10 44 PA11 45 PA12 46 PA13 49 PA14 50 PA15 51 PB0 24 PB1 25 PB2 26 PB3 56 PB4 57 PB5 58 PB6 59 PB7 60 PB8 61 PB9 62 PB10 30 PB11 33 PB12 34 PB13 35 PB14 36 PB15 37 U2STM32G474RETx GND GND GND

1 VDD 16 VDD 32 VSS 15 VDD 48 VSSA 27 VDD 64 VDDA 29 PA0 12 PA1 13 PA2 14 PA3 17 PA4 18 PA5 19 PA6 20 PA7 21 PA8 42 PA9 43 PA10 44 PA11 45 PA12 46 PA13 49 PA14 50 PA15 51 PB0 24 PB1 25 PB2 26 PB3 56 PB4 57 PB5 58 PB6 59 PB7 60 PB8 61 PB9 62 PB10 30 PB11 33 PB12 34 PB13 35 PB14 36 PB15 37 GND

Id: 1/7 Title: Main Board

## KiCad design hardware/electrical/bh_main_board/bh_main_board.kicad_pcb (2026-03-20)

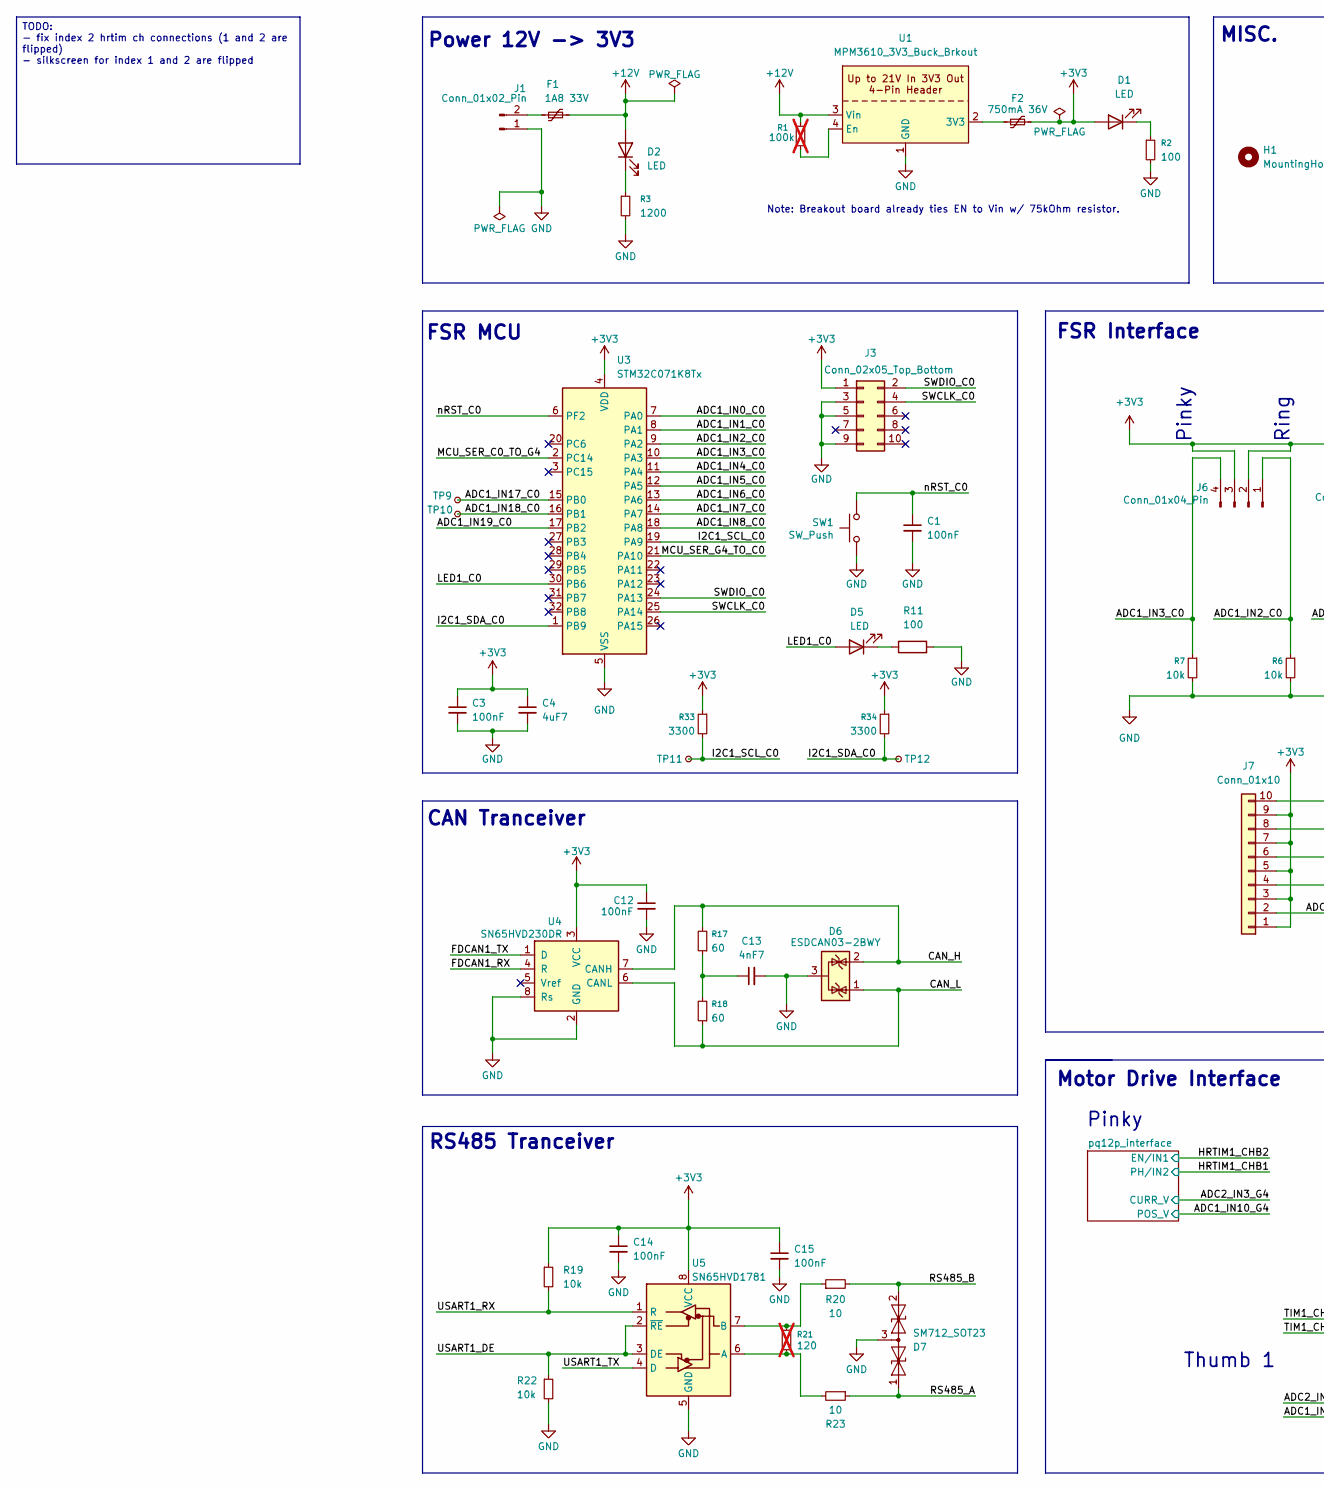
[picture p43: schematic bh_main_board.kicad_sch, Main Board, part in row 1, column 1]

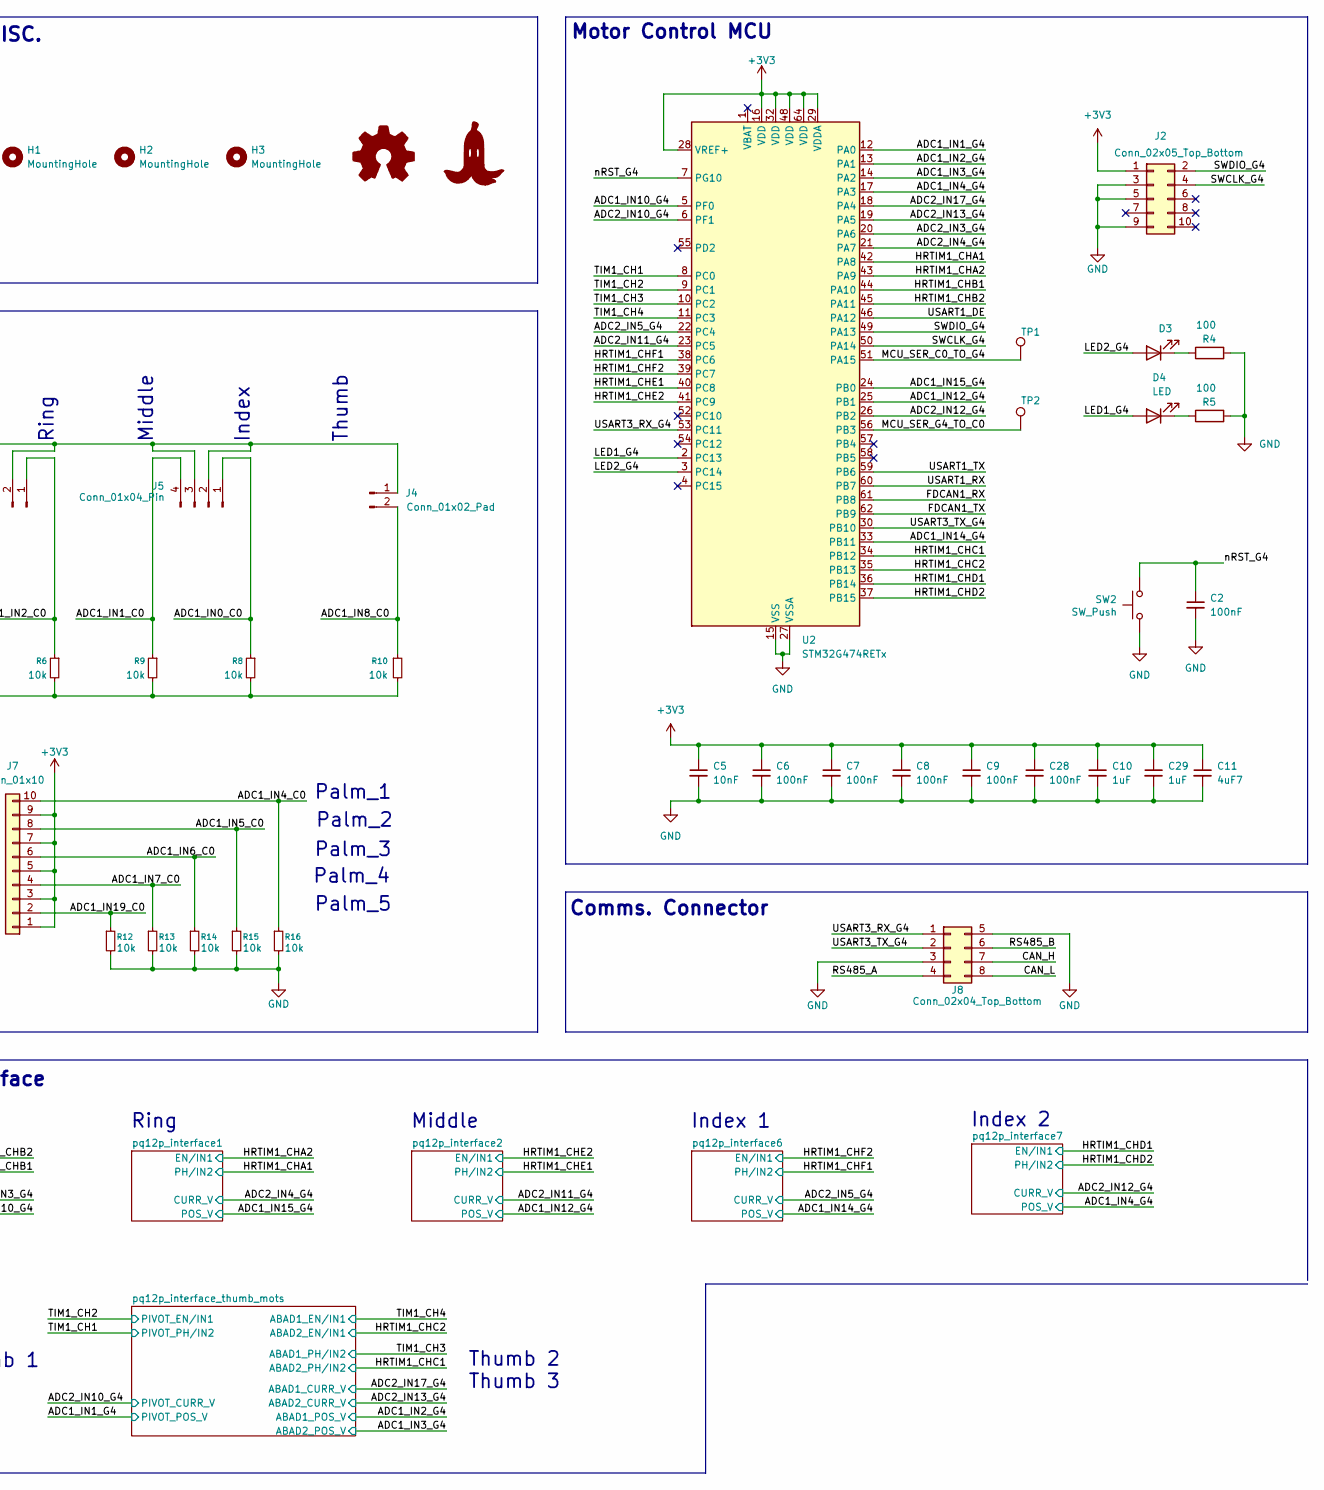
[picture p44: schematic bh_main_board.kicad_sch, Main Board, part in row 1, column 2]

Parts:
ART1: mk_banana_footprint
ART2: Logo_Open_Hardware_Small; OSHW-Logo2_9.8x8mm_SilkScreen
C1, C2, C3, C6, C7, C8, C9, C12, C14, C15, C28: 100nF; C_0402_1005Metric; MFR # GRM155R71H104KE14D; LCSC # C77020
C4, C11: 4uF7; C_0603_1608Metric_Pad1.08x0.95mm_HandSolder; MFR # GRM188R6YA475KE15D; LCSC # C162274
C5: 10nF; C_0402_1005Metric; MFR # GRM155R71H103KA88D; LCSC # C77019
C10, C29: 1uF; C_0603_1608Metric_Pad1.08x0.95mm_HandSolder; MFR # GCM188R71E105KA64D; LCSC # C85862
C13: 4nF7; C_0402_1005Metric; MFR # GRM1555C1H472JE01D; LCSC # C1518204
D1, D2, D3, D4, D5: LED; LED_0402_1005Metric_Pad0.77x0.64mm_HandSolder; MFR # XL-1005UYC; LCSC # C25503856
D6: ESDCAN03-2BWY; SOT-323_SC-70; MFR # ESDCAN03-2BWY; LCSC # C1973833
D7: SM712_SOT23; SOT-23; MFR # SM712-02HTG; LCSC # C172881
F1: 1A8 33V; Fuse_1206_3216Metric_Pad1.42x1.75mm_HandSolder; MFR # YTL 1206L100/33V; LCSC # C49318377
F2: 750mA 36V; Fuse_1206_3216Metric; MFR # 1206L075/36NR; LCSC # C49196638
H1, H2, H3: MountingHole; MountingHole_2.7mm_Pad_Via
J1: Conn_01x02_Pin; AMASS_XT30UPB-M_1x02_P5.0mm_Vertical; MFR # XT30UPB-M; LCSC # C428721
J2, J3: Conn_02x05_Top_Bottom; PinHeader_2x05_P1.27mm_Vertical; MFR # ZX-PZ1.27-2-5PZZ; LCSC # C7501289
J4: Conn_01x02_Pad; JST_ZH_B2B-ZR_1x02_P1.50mm_Vertical; MFR # JST B2B-ZR(LF)(SN); LCSC # C158011
J5, J6: Conn_01x04_Pin; JST_ZH_B4B-ZR_1x04_P1.50mm_Vertical; MFR # JST B4B-ZR(LF)(SN); LCSC # C157997
J7: Conn_01x10; JST_ZH_B10B-ZR_1x10_P1.50mm_Vertical; MFR # B10B-ZR(LF)(SN); LCSC # C158036
J8: Conn_02x04_Top_Bottom; JST_PHD_B8B-PHDSS_2x04_P2.00mm_Vertical; MFR # B8B-PHDSS(LF)(SN); LCSC # C157975
R1: 100k; R_0603_1608Metric_Pad0.98x0.95mm_HandSolder; MFR # RC0603FR-07100KL; LCSC # C14675; not fitted
R2, R4, R5, R11: 100; R_0402_1005Metric_Pad0.72x0.64mm_HandSolder; MFR # ERJ2RKF1000X; LCSC # C413063
R3: 1200; R_0603_1608Metric_Pad0.98x0.95mm_HandSolder; MFR # RC0603FR-071K2L; LCSC # C114605
R6, R7, R8, R9, R10, R12, R13, R14, R15, R16, R19, R22: 10k; R_0402_1005Metric_Pad0.72x0.64mm_HandSolder; MFR # RT0402BRD0710KL; LCSC # C190095
R17, R18: 60; R_0603_1608Metric_Pad0.98x0.95mm_HandSolder; MFR # 0603WAF604JT5E; LCSC # C23090
R20, R23: 10; R_0603_1608Metric_Pad0.98x0.95mm_HandSolder; MFR # RC0603FR-0710RL; LCSC # C109318
R21: 120; R_0603_1608Metric_Pad0.98x0.95mm_HandSolder; MFR # RC0603FR-07120RL; LCSC # C114640; not fitted
R33, R34: 3300; R_0402_1005Metric_Pad0.72x0.64mm_HandSolder; MFR # RC0402FR-073K3L; LCSC # C137992
SW1, SW2: SW_Push; SW_SPST_TS-1088-xR025; MFR # TS-1088R-02526; LCSC # C455281
TP1, TP2: TestPoint; TestPoint_Pad_D1.0mm
TP9, TP10, TP11, TP12: TestPoint_Small; TestPoint_Pad_D2.0mm
U1: MPM3610_3V3_Buck_Brkout; MP3610_3V3_BUCK_BREAKOUT
U2: STM32G474RETx; LQFP-64_10x10mm_P0.5mm; MFR # STM32G474RET6; LCSC # C521608
U3: STM32C071K8Tx; LQFP-32_7x7mm_P0.8mm; MFR # STM32C071K8T6; LCSC # C43650208
U4: SN65HVD230DR; SOIC-8_3.9x4.9mm_P1.27mm; MFR # SN65HVD230DR; LCSC # C12084
U5: SN65HVD1781; SOIC-8_3.9x4.9mm_P1.27mm; MFR # SN65HVD1781DR; LCSC # C42737

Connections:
+3V3: C3.1, C4.1, C5.1, C6.1, C7.1, C8.1, C9.1, C10.1, C11.1, C12.1, C14.1, C15.1, C28.1, C29.1, D1.2 (A), F2.2, J2.1, J3.1, J4.1, J5.2, J5.3, J6.2, J6.3, J7.1, J7.3, J7.5, J7.7, J7.9, R19.1, R33.1, R34.1, U2.16 (VDD), U2.28 (VREF+), U2.29 (VDDA), U2.32 (VDD), U2.48 (VDD), U2.64 (VDD), U3.4 (VDD), U4.3 (VCC), U5.8 (VCC); also elsewhere on the board
+12V: D2.2 (A), F1.2, R1.1, U1.3 (Vin); also elsewhere on the board
/ADC1_IN0_C0: J5.1, R8.1, U3.7 (PA0)
/ADC1_IN1_C0: J5.4, R9.1, U3.8 (PA1)
/ADC1_IN1_G4: U2.12 (PA0); also elsewhere on the board
/ADC1_IN2_C0: J6.1, R6.1, U3.9 (PA2)
/ADC1_IN2_G4: U2.13 (PA1); also elsewhere on the board
/ADC1_IN3_C0: J6.4, R7.1, U3.10 (PA3)
/ADC1_IN3_G4: U2.14 (PA2); also elsewhere on the board
/ADC1_IN4_C0: J7.10, R16.1, U3.11 (PA4)
/ADC1_IN4_G4: U2.17 (PA3); also elsewhere on the board
/ADC1_IN5_C0: J7.8, R15.1, U3.12 (PA5)
/ADC1_IN6_C0: J7.6, R14.1, U3.13 (PA6)
/ADC1_IN7_C0: J7.4, R13.1, U3.14 (PA7)
/ADC1_IN8_C0: J4.2, R10.1, U3.18 (PA8)
/ADC1_IN10_G4: U2.5 (PF0); also elsewhere on the board
/ADC1_IN12_G4: U2.25 (PB1); also elsewhere on the board
/ADC1_IN14_G4: U2.33 (PB11); also elsewhere on the board
/ADC1_IN15_G4: U2.24 (PB0); also elsewhere on the board
/ADC1_IN17_C0: TP9.1, U3.15 (PB0)
/ADC1_IN18_C0: TP10.1, U3.16 (PB1)
/ADC1_IN19_C0: J7.2, R12.1, U3.17 (PB2)
/ADC2_IN3_G4: U2.20 (PA6); also elsewhere on the board
/ADC2_IN4_G4: U2.21 (PA7); also elsewhere on the board
/ADC2_IN5_G4: U2.22 (PC4); also elsewhere on the board
/ADC2_IN10_G4: U2.6 (PF1); also elsewhere on the board
/ADC2_IN11_G4: U2.23 (PC5); also elsewhere on the board
/ADC2_IN12_G4: U2.26 (PB2); also elsewhere on the board
/ADC2_IN13_G4: U2.19 (PA5); also elsewhere on the board
/ADC2_IN17_G4: U2.18 (PA4); also elsewhere on the board
/CAN_H: D6.2 (K), J8.7, R17.2, U4.7 (CANH)
/CAN_L: D6.1 (K), J8.8, R18.1, U4.6 (CANL)
/FDCAN1_RX: U2.61 (PB8), U4.4 (R)
/FDCAN1_TX: U2.62 (PB9), U4.1 (D)
/HRTIM1_CHA1: U2.42 (PA8); also elsewhere on the board
/HRTIM1_CHA2: U2.43 (PA9); also elsewhere on the board
/HRTIM1_CHB1: U2.44 (PA10); also elsewhere on the board
/HRTIM1_CHB2: U2.45 (PA11); also elsewhere on the board
/HRTIM1_CHC1: U2.34 (PB12); also elsewhere on the board
/HRTIM1_CHC2: U2.35 (PB13); also elsewhere on the board
/HRTIM1_CHD1: U2.36 (PB14); also elsewhere on the board
/HRTIM1_CHD2: U2.37 (PB15); also elsewhere on the board
/HRTIM1_CHE1: U2.40 (PC8); also elsewhere on the board
/HRTIM1_CHE2: U2.41 (PC9); also elsewhere on the board
/HRTIM1_CHF1: U2.38 (PC6); also elsewhere on the board
/HRTIM1_CHF2: U2.39 (PC7); also elsewhere on the board
/I2C1_SCL_C0: R33.2, TP11.1, U3.19 (PA9)
/I2C1_SDA_C0: R34.2, TP12.1, U3.1 (PB9)
/LED1_C0: D5.2 (A), U3.30 (PB6)
/LED1_G4: D4.2 (A), U2.2 (PC13)
/LED2_G4: D3.2 (A), U2.3 (PC14)
/MCU_SER_C0_TO_G4: TP1.1, U2.51 (PA15), U3.2 (PC14)
/MCU_SER_G4_TO_C0: TP2.1, U2.56 (PB3), U3.21 (PA10)
/RS485_A: D7.1 (A1), J8.4, R23.1
/RS485_B: D7.2 (A2), J8.6, R20.2
/SWCLK_C0: J3.4, U3.25 (PA14)
/SWCLK_G4: J2.4, U2.50 (PA14)
/SWDIO_C0: J3.2, U3.24 (PA13)
/SWDIO_G4: J2.2, U2.49 (PA13)
/TIM1_CH1: U2.8 (PC0); also elsewhere on the board
/TIM1_CH2: U2.9 (PC1); also elsewhere on the board
/TIM1_CH3: U2.10 (PC2); also elsewhere on the board
/TIM1_CH4: U2.11 (PC3); also elsewhere on the board
/USART1_DE: R22.1, U2.46 (PA12), U5.2 (~RE), U5.3 (DE)
/USART1_RX: R19.2, U2.60 (PB7), U5.1 (R)
/USART1_TX: U2.59 (PB6), U5.4 (D)
/USART3_RX_G4: J8.1, U2.53 (PC11)
/USART3_TX_G4: J8.2, U2.30 (PB10)
/nRST_C0: C1.1, SW1.2, U3.6 (PF2)
/nRST_G4: C2.1, SW2.2, U2.7 (PG10)
GND: C1.2, C2.2, C3.2, C4.2, C5.2, C6.2, C7.2, C8.2, C9.2, C10.2, C11.2, C12.2, C13.2, C14.2, C15.2, C28.2, C29.2, D6.3 (A), D7.3 (common), J1.1, J2.3, J2.5, J2.9, J3.3, J3.5, J3.9, J8.3, J8.5, R2.2, R3.2, R4.2, R5.2, R6.2, R7.2, R8.2, R9.2, R10.2, R11.2, R12.2, R13.2, R14.2, R15.2, R16.2, R22.2, SW1.1, SW2.1, U1.1 (GND), U2.15 (VSS), U2.27 (VSSA), U2.31 (VSS), U2.47 (VSS), U2.63 (VSS), U3.5 (VSS), U4.2 (GND), U4.8 (Rs), U5.5 (GND); also elsewhere on the board
unnamed: C13.1, R17.1, R18.2
unnamed: D1.1 (K), R2.1
unnamed: D2.1 (K), R3.1
unnamed: D3.1 (K), R4.1
unnamed: D4.1 (K), R5.1
unnamed: D5.1 (K), R11.1
unnamed: F1.1, J1.2
unnamed: F2.1, U1.2 (3V3)
unnamed: R1.2, U1.4 (En)
unnamed: R21.2, R23.2, U5.6 (A)
unnamed: R20.1, R21.1, U5.7 (B)

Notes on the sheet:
Motor Drive Interface
Palm_3
Thumb 2
Pinky
Thumb 3
Index 2
CAN Tranceiver
FSR Interface
Palm_4
Motor Control MCU
RS485 Tranceiver
Middle
Comms. Connector
Ring
Thumb 1
Palm_5
Note: Breakout board already ties EN to Vin w/ 75kOhm resistor.
Power 12V -> 3V3
Index
Palm_1
MISC.
FSR MCU
Palm_2
Index 1
Thumb
TODO: - fix index 2 hrtim ch connections (1 and 2 are flipped) - silkscreen for index 1 and 2 are flipped

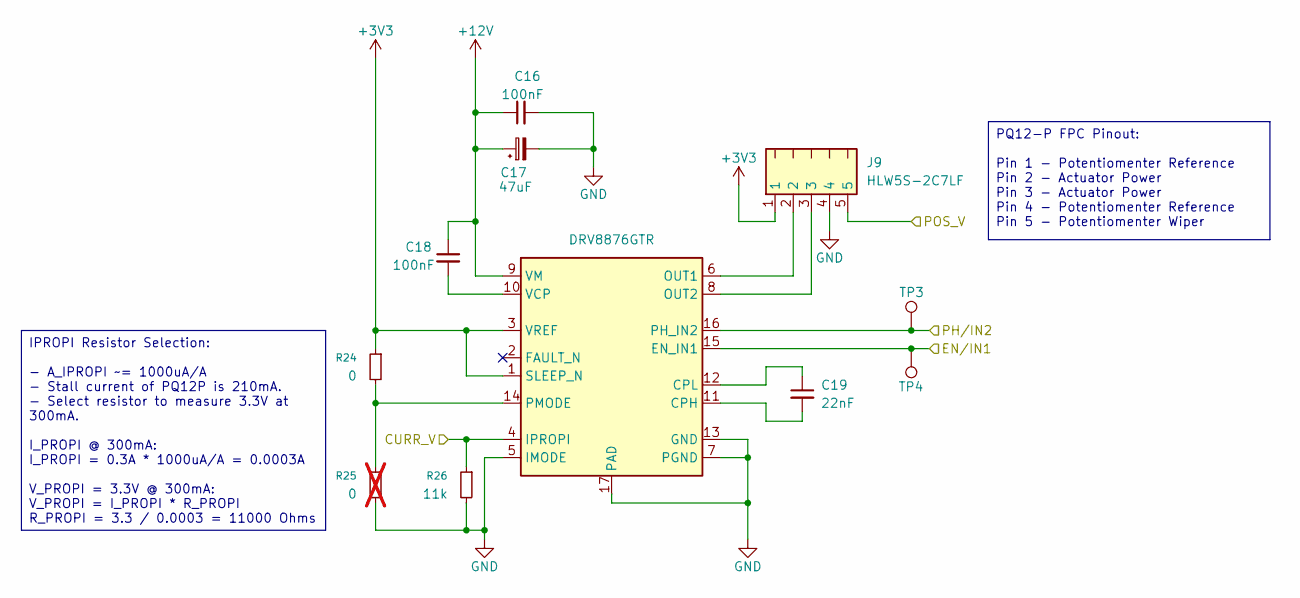
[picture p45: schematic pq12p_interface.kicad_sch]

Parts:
C16, C18: 100nF; C_0402_1005Metric; MFR # GRM155R71H104KE14D; LCSC # C77020
C17: 47uF; CP_Elec_6.3x5.8; MFR # EEEFP1V470AP; LCSC # C401754
C19: 22nF; C_0402_1005Metric; MFR # GRM155R71H223KA12D; LCSC # C77023
J9: HLW5S-2C7LF; MFR # HLW5S-2C7LF; LCSC # C5406437
R24: 0; R_0603_1608Metric_Pad0.98x0.95mm_HandSolder; MFR # RC0603JR-070RL; LCSC # C95177
R25: 0; R_0603_1608Metric_Pad0.98x0.95mm_HandSolder; MFR # RC0603JR-070RL; LCSC # C95177; not fitted
R26: 11k; R_0402_1005Metric_Pad0.72x0.64mm_HandSolder; MFR # RT0402BRE0711KL; LCSC # C705643
TP3, TP4: TestPoint; TestPoint_Pad_D1.0mm
U6: DRV8876GTR; DRV8876GTR-MFG; MFR # DRV8876RGTR; LCSC # C1852100

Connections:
+3V3: J9.1, R24.1, U6.1 (SLEEP_N), U6.3 (VREF); also elsewhere on the board
+12V: C16.1, C17.1, C18.1, U6.9 (VM); also elsewhere on the board
/ADC1_IN10_G4: J9.5; also elsewhere on the board
/ADC2_IN3_G4: R26.1, U6.4 (IPROPI); also elsewhere on the board
/HRTIM1_CHB1: TP3.1, U6.16 (PH_IN2); also elsewhere on the board
/HRTIM1_CHB2: TP4.1, U6.15 (EN_IN1); also elsewhere on the board
GND: C16.2, C17.2, J9.4, R25.2, R26.2, U6.5 (IMODE), U6.7 (PGND), U6.13 (GND), U6.17 (PAD), U6.18, U6.19, U6.20, U6.21, U6.22; also elsewhere on the board
unnamed: C19.2, U6.11 (CPH)
unnamed: C19.1, U6.12 (CPL)
unnamed: J9.2, U6.6 (OUT1)
unnamed: J9.3, U6.8 (OUT2)
unnamed: R24.2, R25.1, U6.14 (PMODE)
unnamed: C18.2, U6.10 (VCP)

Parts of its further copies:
C20, C22, C24, C26, C36, C38, C40, C42: 100nF; C_0402_1005Metric; MFR # GRM155R71H104KE14D; LCSC # C77020
C21, C25, C37, C41: 47uF; CP_Elec_6.3x5.8; MFR # EEEFP1V470AP; LCSC # C401754
C23, C27, C39, C43: 22nF; C_0402_1005Metric; MFR # GRM155R71H223KA12D; LCSC # C77023
J10, J11, J12, J13: HLW5S-2C7LF; MFR # HLW5S-2C7LF; LCSC # C5406437
R27, R30, R39, R42: 0; R_0603_1608Metric_Pad0.98x0.95mm_HandSolder; MFR # RC0603JR-070RL; LCSC # C95177
R28, R31, R40, R43: 0; R_0603_1608Metric_Pad0.98x0.95mm_HandSolder; MFR # RC0603JR-070RL; LCSC # C95177; not fitted
R29, R32, R41, R44: 11k; R_0402_1005Metric_Pad0.72x0.64mm_HandSolder; MFR # RT0402BRE0711KL; LCSC # C705643
TP5, TP6, TP7, TP8, TP13, TP14, TP15, TP16: TestPoint; TestPoint_Pad_D1.0mm
U7, U8, U11, U12: DRV8876GTR; DRV8876GTR-MFG; MFR # DRV8876RGTR; LCSC # C1852100

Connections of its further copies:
+3V3: J10.1, J11.1, J12.1, J13.1, R27.1, R30.1, R39.1, R42.1, U7.1 (SLEEP_N), U7.3 (VREF), U8.1 (SLEEP_N), U8.3 (VREF), U11.1 (SLEEP_N), U11.3 (VREF), U12.1 (SLEEP_N), U12.3 (VREF); also elsewhere on the board
+12V: C20.1, C21.1, C22.1, C24.1, C25.1, C26.1, C36.1, C37.1, C38.1, C40.1, C41.1, C42.1, U7.9 (VM), U8.9 (VM), U11.9 (VM), U12.9 (VM); also elsewhere on the board
/ADC1_IN4_G4: J13.5; also elsewhere on the board
/ADC1_IN12_G4: J11.5; also elsewhere on the board
/ADC1_IN14_G4: J12.5; also elsewhere on the board
/ADC1_IN15_G4: J10.5; also elsewhere on the board
/ADC2_IN4_G4: R29.1, U7.4 (IPROPI); also elsewhere on the board
/ADC2_IN5_G4: R41.1, U11.4 (IPROPI); also elsewhere on the board
/ADC2_IN11_G4: R32.1, U8.4 (IPROPI); also elsewhere on the board
/ADC2_IN12_G4: R44.1, U12.4 (IPROPI); also elsewhere on the board
/HRTIM1_CHA1: TP5.1, U7.16 (PH_IN2); also elsewhere on the board
/HRTIM1_CHA2: TP6.1, U7.15 (EN_IN1); also elsewhere on the board
/HRTIM1_CHD1: TP16.1, U12.15 (EN_IN1); also elsewhere on the board
/HRTIM1_CHD2: TP15.1, U12.16 (PH_IN2); also elsewhere on the board
/HRTIM1_CHE1: TP7.1, U8.16 (PH_IN2); also elsewhere on the board
/HRTIM1_CHE2: TP8.1, U8.15 (EN_IN1); also elsewhere on the board
/HRTIM1_CHF1: TP13.1, U11.16 (PH_IN2); also elsewhere on the board
/HRTIM1_CHF2: TP14.1, U11.15 (EN_IN1); also elsewhere on the board
GND: C20.2, C21.2, C24.2, C25.2, C36.2, C37.2, C40.2, C41.2, J10.4, J11.4, J12.4, J13.4, R28.2, R29.2, R31.2, R32.2, R40.2, R41.2, R43.2, R44.2, U7.5 (IMODE), U7.7 (PGND), U7.13 (GND), U7.17 (PAD), U7.18, U7.19, U7.20, U7.21, U7.22, U8.5 (IMODE), U8.7 (PGND), U8.13 (GND), U8.17 (PAD), U8.18, U8.19, U8.20, U8.21, U8.22, U11.5 (IMODE), U11.7 (PGND), U11.13 (GND), U11.17 (PAD), U11.18, U11.19, U11.20, U11.21, U11.22, U12.5 (IMODE), U12.7 (PGND), U12.13 (GND), U12.17 (PAD), U12.18, U12.19, U12.20, U12.21, U12.22; also elsewhere on the board
unnamed: C23.2, U7.11 (CPH)
unnamed: C23.1, U7.12 (CPL)
unnamed: J10.2, U7.6 (OUT1)
unnamed: J10.3, U7.8 (OUT2)
unnamed: R27.2, R28.1, U7.14 (PMODE)
unnamed: C22.2, U7.10 (VCP)
unnamed: C27.2, U8.11 (CPH)
unnamed: C27.1, U8.12 (CPL)
unnamed: J11.2, U8.6 (OUT1)
unnamed: J11.3, U8.8 (OUT2)
unnamed: R30.2, R31.1, U8.14 (PMODE)
unnamed: C26.2, U8.10 (VCP)
unnamed: C39.2, U11.11 (CPH)
unnamed: C39.1, U11.12 (CPL)
unnamed: J12.2, U11.6 (OUT1)
unnamed: J12.3, U11.8 (OUT2)
unnamed: R39.2, R40.1, U11.14 (PMODE)
unnamed: C38.2, U11.10 (VCP)
unnamed: C43.2, U12.11 (CPH)
unnamed: C43.1, U12.12 (CPL)
unnamed: J13.2, U12.6 (OUT1)
unnamed: J13.3, U12.8 (OUT2)
unnamed: R42.2, R43.1, U12.14 (PMODE)
unnamed: C42.2, U12.10 (VCP)

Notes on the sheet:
PQ12-P FPC Pinout: Pin 1 - Potentiomenter Reference Pin 2 - Actuator Power Pin 3 - Actuator Power Pin 4 - Potentiomenter Reference Pin 5 - Potentiomenter Wiper
IPROPI Resistor Selection: - A_IPROPI ~= 1000uA/A - Stall current of PQ12P is 210mA. - Select resistor to measure 3.3V at 300mA. I_PROPI @ 300mA: I_PROPI = 0.3A * 1000uA/A = 0.0003A V_PROPI = 3.3V @ 300mA: V_PROPI = I_PROPI * R_PROPI R_PROPI = 3.3 / 0.0003 = 11000 Ohms

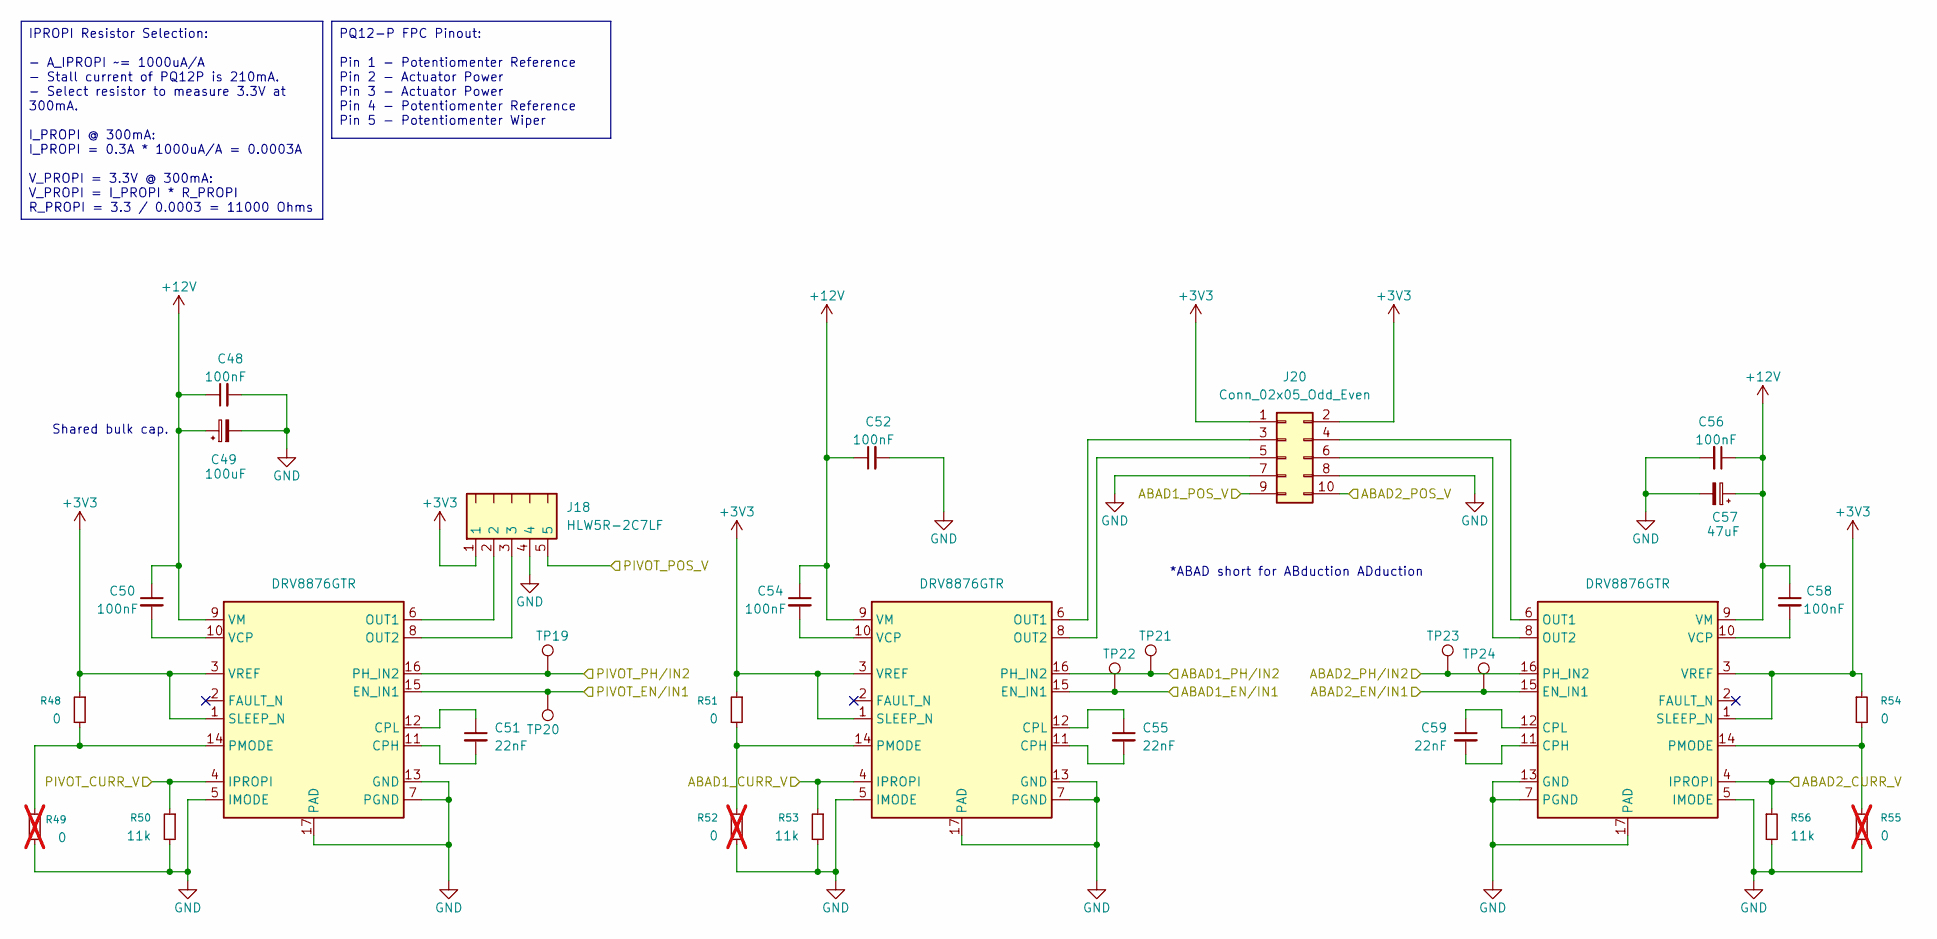
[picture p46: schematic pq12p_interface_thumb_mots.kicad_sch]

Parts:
C48, C50, C52, C54, C56, C58: 100nF; C_0402_1005Metric; MFR # GRM155R71H104KE14D; LCSC # C77020
C49: 100uF; CP_Elec_6.3x5.8; MFR # EEEFT1V101AP; LCSC # C128464
C51, C55, C59: 22nF; C_0402_1005Metric; MFR # GRM155R71H223KA12D; LCSC # C77023
C57: 47uF; CP_Elec_6.3x5.8; MFR # EEEFP1V470AP; LCSC # C401754
J18: HLW5R-2C7LF; MFR # HLW5R-2C7LF; LCSC # C5406452
J20: Conn_02x05_Odd_Even; JST_PHD_B10B-PHDSS_2x05_P2.00mm_Vertical; MFR # B10B-PHDSS(LF)(SN); LCSC # C471519
R48, R51, R54: 0; R_0603_1608Metric_Pad0.98x0.95mm_HandSolder; MFR # RC0603JR-070RL; LCSC # C95177
R49, R52, R55: 0; R_0603_1608Metric_Pad0.98x0.95mm_HandSolder; MFR # RC0603JR-070RL; LCSC # C95177; not fitted
R50, R53, R56: 11k; R_0402_1005Metric_Pad0.72x0.64mm_HandSolder; MFR # RT0402BRE0711KL; LCSC # C705643
TP19, TP20, TP21, TP22, TP23, TP24: TestPoint; TestPoint_Pad_D1.0mm
U14, U15, U16: DRV8876GTR; DRV8876GTR-MFG; MFR # DRV8876RGTR; LCSC # C1852100

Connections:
+3V3: J18.1, J20.1, J20.2, R48.1, R51.1, R54.1, U14.1 (SLEEP_N), U14.3 (VREF), U15.1 (SLEEP_N), U15.3 (VREF), U16.1 (SLEEP_N), U16.3 (VREF); also elsewhere on the board
+12V: C48.1, C49.1, C50.1, C52.1, C54.1, C56.1, C57.1, C58.1, U14.9 (VM), U15.9 (VM), U16.9 (VM); also elsewhere on the board
/ADC1_IN1_G4: J18.5; also elsewhere on the board
/ADC1_IN2_G4: J20.9; also elsewhere on the board
/ADC1_IN3_G4: J20.10; also elsewhere on the board
/ADC2_IN10_G4: R50.1, U14.4 (IPROPI); also elsewhere on the board
/ADC2_IN13_G4: R56.1, U16.4 (IPROPI); also elsewhere on the board
/ADC2_IN17_G4: R53.1, U15.4 (IPROPI); also elsewhere on the board
/HRTIM1_CHC1: TP23.1, U16.16 (PH_IN2); also elsewhere on the board
/HRTIM1_CHC2: TP24.1, U16.15 (EN_IN1); also elsewhere on the board
/TIM1_CH1: TP19.1, U14.16 (PH_IN2); also elsewhere on the board
/TIM1_CH2: TP20.1, U14.15 (EN_IN1); also elsewhere on the board
/TIM1_CH3: TP21.1, U15.16 (PH_IN2); also elsewhere on the board
/TIM1_CH4: TP22.1, U15.15 (EN_IN1); also elsewhere on the board
GND: C48.2, C49.2, C52.2, C56.2, C57.2, J18.4, J20.7, J20.8, R49.2, R50.2, R52.2, R53.2, R55.2, R56.2, U14.5 (IMODE), U14.7 (PGND), U14.13 (GND), U14.17 (PAD), U14.18, U14.19, U14.20, U14.21, U14.22, U15.5 (IMODE), U15.7 (PGND), U15.13 (GND), U15.17 (PAD), U15.18, U15.19, U15.20, U15.21, U15.22, U16.5 (IMODE), U16.7 (PGND), U16.13 (GND), U16.17 (PAD), U16.18, U16.19, U16.20, U16.21, U16.22; also elsewhere on the board
unnamed: J20.3, U15.6 (OUT1)
unnamed: J20.4, U16.6 (OUT1)
unnamed: J20.5, U15.8 (OUT2)
unnamed: J20.6, U16.8 (OUT2)
unnamed: C51.2, U14.11 (CPH)
unnamed: C51.1, U14.12 (CPL)
unnamed: J18.2, U14.6 (OUT1)
unnamed: J18.3, U14.8 (OUT2)
unnamed: R48.2, R49.1, U14.14 (PMODE)
unnamed: C50.2, U14.10 (VCP)
unnamed: C55.2, U15.11 (CPH)
unnamed: C55.1, U15.12 (CPL)
unnamed: R51.2, R52.1, U15.14 (PMODE)
unnamed: C54.2, U15.10 (VCP)
unnamed: C59.2, U16.11 (CPH)
unnamed: C59.1, U16.12 (CPL)
unnamed: R54.2, R55.1, U16.14 (PMODE)
unnamed: C58.2, U16.10 (VCP)

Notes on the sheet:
*ABAD short for ABduction ADduction
Shared bulk cap.
PQ12-P FPC Pinout: Pin 1 - Potentiomenter Reference Pin 2 - Actuator Power Pin 3 - Actuator Power Pin 4 - Potentiomenter Reference Pin 5 - Potentiomenter Wiper
IPROPI Resistor Selection: - A_IPROPI ~= 1000uA/A - Stall current of PQ12P is 210mA. - Select resistor to measure 3.3V at 300mA. I_PROPI @ 300mA: I_PROPI = 0.3A * 1000uA/A = 0.0003A V_PROPI = 3.3V @ 300mA: V_PROPI = I_PROPI * R_PROPI R_PROPI = 3.3 / 0.0003 = 11000 Ohms

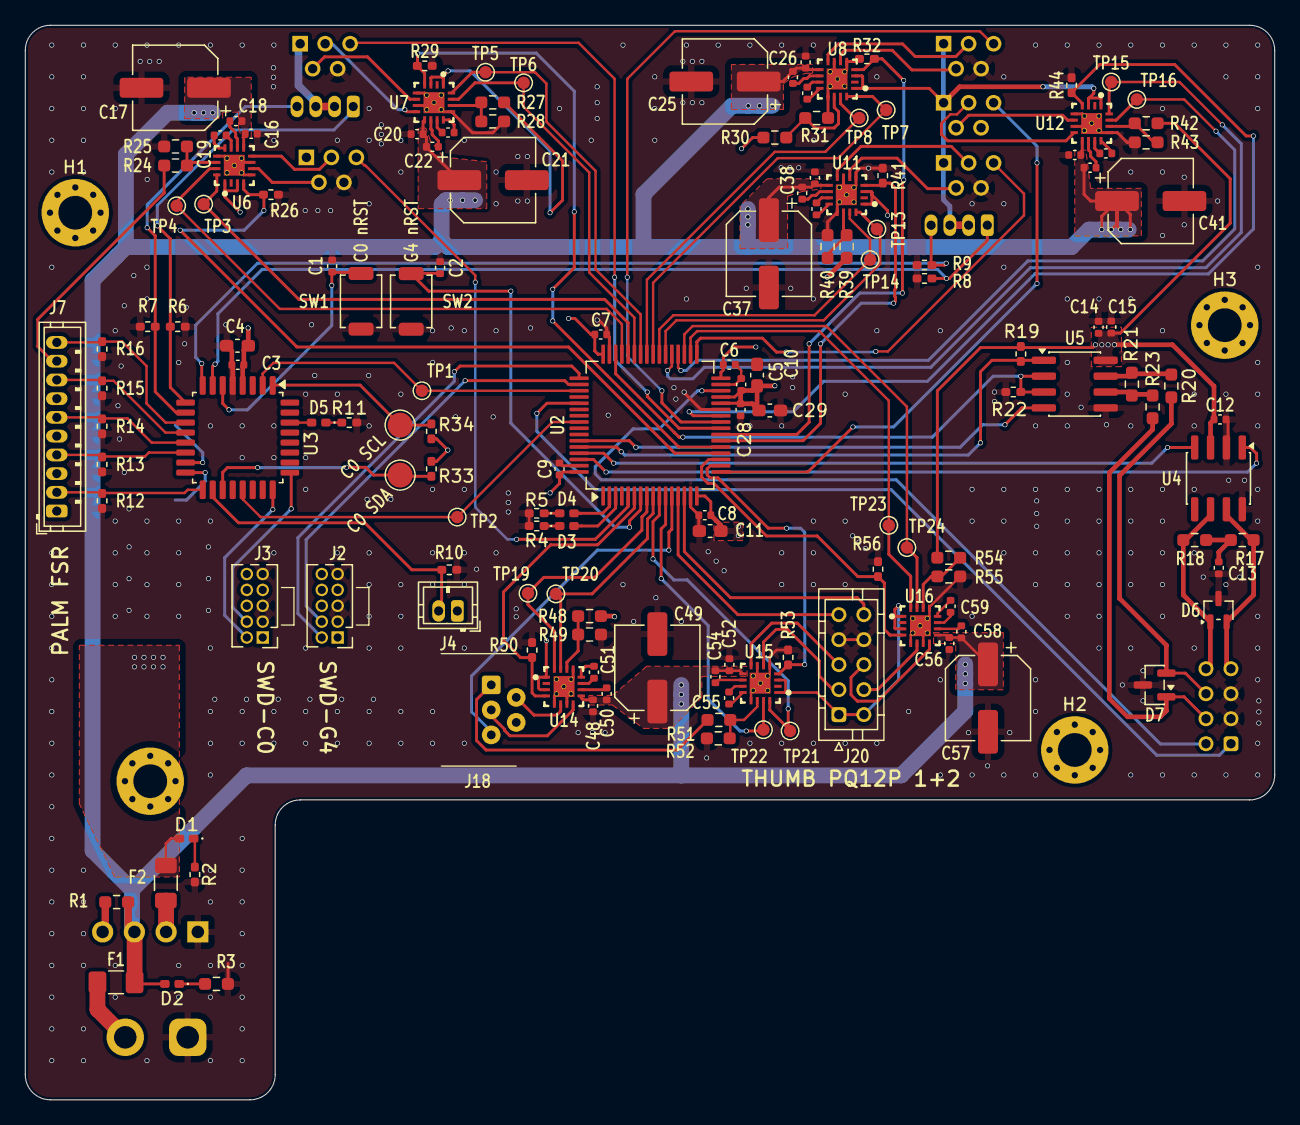
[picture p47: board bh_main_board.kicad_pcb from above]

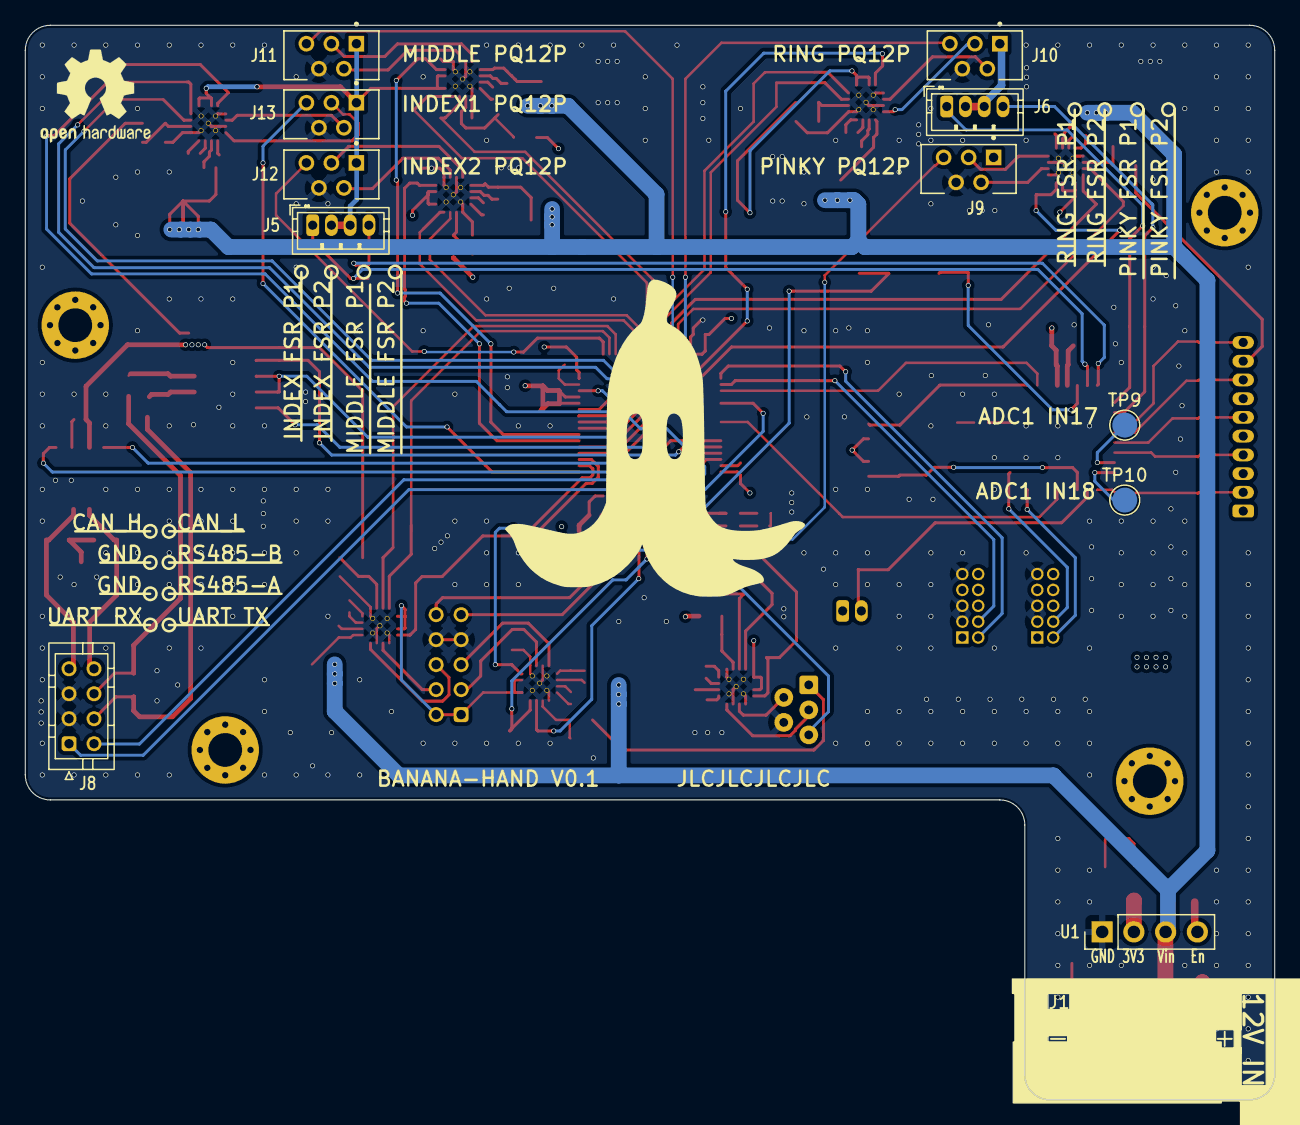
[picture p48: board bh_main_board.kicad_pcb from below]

Board: 4 copper layers, 100.0 x 86.0 mm, 163 parts (14 on the bottom side), 130 nets.

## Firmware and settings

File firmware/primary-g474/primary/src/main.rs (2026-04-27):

#![no_std]
#![no_main]

mod board_map;
mod c0_reader;
mod command_reader;
mod config;
mod control_config;
mod current_reader;
mod fmt;
mod motor_control;
mod pid;
mod position_reader;
mod protocol;
mod shared;
mod telemetry_sender;

#[cfg(not(feature = "defmt"))]
use panic_halt as _;

#[cfg(feature = "defmt")]
use {defmt_rtt as _, panic_probe as _};

use embassy_executor::Spawner;
use embassy_stm32::bind_interrupts;
use embassy_stm32::time::khz;
use embassy_stm32::{
    Config,
    adc::{Adc, AdcConfig},
    gpio::OutputType,
    rcc::{APBPrescaler, clocks},
    time::Hertz,
    timer::simple_pwm::{PwmPin, SimplePwm},
    usart::{Config as UartConfig, Uart, UartRx},
};
use embassy_time::{Duration, Ticker};
use hrtim_pwm_hal::{HrtimCore, HrtimPrescaler, period_reg_val};

use banana_hand_common::FORCE_SENS_BAUD;
use board_map::{MotorPwm, current_adc_pins, position_adc_pins};
use config::{COMMAND_COUNT, CURRENT_COUNT, FORCE_COUNT, POSITION_COUNT};
use control_config::{
    CONTROL_HZ, CommandInputs, ControlMode, DEFAULT_CONTROL_MODE, ForceInputs, PositionInputs,
};
use motor_control::{Controller, MotorCommand, MotorOutputs};
use protocol::TELEM_BAUD;
use shared::{SharedData, SharedMode};

bind_interrupts!(struct Irqs {
    USART2 => embassy_stm32::usart::InterruptHandler<embassy_stm32::peripherals::USART2>;
    USART3 => embassy_stm32::usart::InterruptHandler<embassy_stm32::peripherals::USART3>;
});

static SHARED_POSITIONS: SharedData<POSITION_COUNT> = SharedData::new();
static SHARED_CURRENTS: SharedData<CURRENT_COUNT> = SharedData::new();
static SHARED_POSITION_COMMANDS: SharedData<COMMAND_COUNT> = SharedData::new();
static SHARED_FORCE_COMMANDS: SharedData<COMMAND_COUNT> = SharedData::new();
static SHARED_CONTROL_MODE: SharedMode = SharedMode::new(DEFAULT_CONTROL_MODE.to_wire());
static SHARED_FORCE: SharedData<FORCE_COUNT> = SharedData::new();
const PWM_FREQ: Hertz = Hertz(20_000);

fn coast_all_outputs() -> MotorOutputs {
    MotorOutputs {
        ring: MotorCommand::Coast,
        pinky: MotorCommand::Coast,
        thumb_flex: MotorCommand::Coast,
        index1: MotorCommand::Coast,
        middle: MotorCommand::Coast,
        thumb_revolve: MotorCommand::Coast,
    }
}

#[embassy_executor::main]
async fn main(_spawner: Spawner) {
    let mut config = Config::default();
    {
        use embassy_stm32::rcc::*;
        config.rcc.pll = Some(Pll {
            source: PllSource::HSI,
            prediv: PllPreDiv::DIV4,
            mul: PllMul::MUL85,
            divp: None,
            divq: None,
            // Main system clock at 170 MHz
            divr: Some(PllRDiv::DIV2),
        });
        config.rcc.mux.adc12sel = mux::Adcsel::SYS;
        config.rcc.sys = Sysclk::PLL1_R;
        config.rcc.ls = LsConfig::default_lsi();
    }
    let p = embassy_stm32::init(config);
    SHARED_CONTROL_MODE.write(DEFAULT_CONTROL_MODE.to_wire());

    // USART3: PC link (kept off PA2/PA3 because those are used as potentiometer inputs).
    let mut uart3_config = UartConfig::default();
    uart3_config.baudrate = TELEM_BAUD;
    let uart3 = Uart::new(
        p.USART3,
        p.PC11, // RX pin (PC -> MCU)
        p.PB10, // TX pin (MCU -> PC)
        Irqs,
        p.DMA1_CH6, // TX DMA channel
        p.DMA1_CH5, // RX DMA channel
        uart3_config,
    )
    .unwrap();

    let (tx3, rx3) = uart3.split();
    _spawner
        .spawn(telemetry_sender::telemetry_sender_task(
            tx3,
            &SHARED_POSITIONS,
            &SHARED_FORCE,
            &SHARED_CURRENTS,
        ))
        .unwrap();
    _spawner
        .spawn(command_reader::command_reader_task(
            rx3,
            &SHARED_POSITION_COMMANDS,
            &SHARED_FORCE_COMMANDS,
            &SHARED_CONTROL_MODE,
        ))
        .unwrap();

    // USART2: C0 force reader (RX only).
    let mut uart1_config = UartConfig::default();
    uart1_config.baudrate = FORCE_SENS_BAUD;

    // RX on PA15 from C0 USART1_TX (PB6).
    let uart1_rx = UartRx::new(p.USART2, Irqs, p.PA15, p.DMA1_CH1, uart1_config).unwrap();

    _spawner
        .spawn(c0_reader::c0_reader_task(uart1_rx, &SHARED_FORCE))
        .unwrap();

    // ADC + position reader (G4 pots).
    let dma = p.DMA1_CH2;
    let adc = Adc::new(p.ADC1, AdcConfig::default());
    let pos_pins = position_adc_pins(p.PA0, p.PA1, p.PA2, p.PA3, p.PB0, p.PB1, p.PB11, p.PF0);
    _spawner
        .spawn(position_reader::position_reader_task(
            adc,
            dma,
            pos_pins,
            &SHARED_POSITIONS,
        ))
        .unwrap();

    // ADC2 + current reader (same logical order as positions/commands).
    let current_dma = p.DMA2_CH1;
    let current_adc = Adc::new(p.ADC2, AdcConfig::default());
    let current_pins = current_adc_pins(p.PA4, p.PA5, p.PA6, p.PA7, p.PB2, p.PC4, p.PC5, p.PF1);
    _spawner
        .spawn(current_reader::current_reader_task(
            current_adc,
            current_dma,
            current_pins,
            &SHARED_CURRENTS,
        ))
        .unwrap();

    let prescaler = HrtimPrescaler::DIV32;
    let period = period_reg_val(clocks(&p.RCC), APBPrescaler::DIV1, prescaler, PWM_FREQ).unwrap();

    // TIM1 pin/channel contract:
    // CH1=PC0 and CH2=PC1 drive thumb-revolve H-bridge.
    // CH3=PC2 and CH4=PC3 are kept enabled but currently unused.
    let thumb_revolve_ch1_pin = PwmPin::new(p.PC0, OutputType::PushPull); // TIM1_CH1
    let thumb_revolve_ch2_pin = PwmPin::new(p.PC1, OutputType::PushPull); // TIM1_CH2
    let thumb_flex_unused_ch1_pin = PwmPin::new(p.PC2, OutputType::PushPull); // TIM1_CH3 (unused)
    let thumb_flex_unused_ch2_pin = PwmPin::new(p.PC3, OutputType::PushPull); // TIM1_CH4 (unused)
    let thumb_pwm = SimplePwm::new(
        p.TIM1,
        Some(thumb_revolve_ch1_pin),
        Some(thumb_revolve_ch2_pin),
        Some(thumb_flex_unused_ch1_pin),
        Some(thumb_flex_unused_ch2_pin),
        khz(20),
        Default::default(),
    );
    let thumb_pwm_ch = thumb_pwm.split();

    // HRTIM channels mapped directly to actuators.
    let (ring, pinky, thumb_flex, index1, middle, index2_unused) = HrtimCore::new()
        .add_tim_a_ch1_ch2(p.PA8, p.PA9, period, prescaler)
        .add_tim_b_ch1_ch2(p.PA10, p.PA11, period, prescaler)
        .add_tim_c_ch1_ch2(p.PB12, p.PB13, period, prescaler)
        .add_tim_d_ch1_ch2(p.PB14, p.PB15, period, prescaler)
        .add_tim_e_ch1_ch2(p.PC8, p.PC9, period, prescaler)
        .add_tim_f_ch1_ch2(p.PC6, p.PC7, period, prescaler)
        .split_active()
        .unwrap();

    let mut motor_pwm = MotorPwm::new(
        ring,
        pinky,
        thumb_flex,
        index1,
        middle,
        index2_unused,
        thumb_pwm_ch.ch1, // TIM1_CH1 -> PC0 -> thumb_revolve_ch1
        thumb_pwm_ch.ch2, // TIM1_CH2 -> PC1 -> thumb_revolve_ch2
        thumb_pwm_ch.ch3, // TIM1_CH3 -> PC2 -> unused
        thumb_pwm_ch.ch4, // TIM1_CH4 -> PC3 -> unused
    );

    let mut controller = Controller::default();
    let mut control_ticker = Ticker::every(Duration::from_hz(CONTROL_HZ));
    let mut applied_mode = DEFAULT_CONTROL_MODE;
    let mut waiting_for_fresh_command = false;
    let mut required_command_seq = SHARED_POSITION_COMMANDS.seq();

    // MAIN PID LOOP //
    loop {
        let requested_mode =
            ControlMode::from_wire(SHARED_CONTROL_MODE.read()).unwrap_or(DEFAULT_CONTROL_MODE);

        if requested_mode != applied_mode {
            let latest_positions = SHARED_POSITIONS.read_snapshot();
            let latest_force = SHARED_FORCE.read_snapshot();
            let latest_position_commands = SHARED_POSITION_COMMANDS.read_snapshot();
            let latest_force_commands = SHARED_FORCE_COMMANDS.read_snapshot();

            defmt::info!(
                "mode change: {} -> {}, position_cmds: {}, force_cmds: {}, positions: {}, forces: {}",
                applied_mode.to_wire(),
                requested_mode.to_wire(),
                latest_position_commands,
                latest_force_commands,
                latest_positions,
                latest_force
            );

            controller.set_mode(requested_mode);
            applied_mode = requested_mode;
            waiting_for_fresh_command = true;
            required_command_seq = match applied_mode {
                ControlMode::Position => SHARED_POSITION_COMMANDS.seq(),
                ControlMode::Force => SHARED_FORCE_COMMANDS.seq(),
            };
        }

        let latest_force = SHARED_FORCE.read_snapshot();
        let latest_positions = SHARED_POSITIONS.read_snapshot();
        let position_commands = SHARED_POSITION_COMMANDS.read_snapshot();
        let force_commands = SHARED_FORCE_COMMANDS.read_snapshot();

        let active_command_seq = match applied_mode {
            ControlMode::Position => SHARED_POSITION_COMMANDS.seq(),
            ControlMode::Force => SHARED_FORCE_COMMANDS.seq(),
        };

        if waiting_for_fresh_command && active_command_seq != required_command_seq {
            waiting_for_fresh_command = false;
        }

        let active_commands = match applied_mode {
            ControlMode::Position => &position_commands,
            ControlMode::Force => &force_commands,
        };

        let command_inputs = CommandInputs::from_raw(active_commands);
        let position_inputs = PositionInputs::from_raw(&latest_positions);
        let force_inputs = ForceInputs::from_raw(&latest_force);

        let outputs = if waiting_for_fresh_command {
            coast_all_outputs()
        } else {
            controller.step(&command_inputs, &position_inputs, &force_inputs)
        };
        let pwm_outputs = outputs.into_pwm_outputs();
        motor_pwm.apply_outputs(pwm_outputs);

        control_ticker.next().await;
    }
}

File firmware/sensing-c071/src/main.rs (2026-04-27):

#![no_std]
#![no_main]

mod fmt;
// mod force_sensor;

#[cfg(not(feature = "defmt"))]
use panic_halt as _;
#[cfg(feature = "defmt")]
use {defmt_rtt as _, panic_probe as _};

use banana_hand_common::{
    FORCE_DATA_PACKET_LEN, FORCE_SENS_BAUD, FORCE_SENSOR_COUNT, FORCE_SENSOR_INDEX_IDX,
    FORCE_SENSOR_MIDDLE_IDX, FORCE_SENSOR_PALM_1_IDX, FORCE_SENSOR_PALM_2_IDX, FORCE_SENSOR_PALM_3_IDX,
    FORCE_SENSOR_PALM_4_IDX, FORCE_SENSOR_PALM_5_IDX, FORCE_SENSOR_PINKY_IDX, FORCE_SENSOR_RING_IDX,
    FORCE_SENSOR_THUMB_IDX, encode_readings_unchecked,
};
use embassy_executor::Spawner;
use embassy_stm32::adc::{Adc, AdcChannel, AnyAdcChannel, Resolution, SampleTime};
use embassy_stm32::usart::{Config as UartConfig, UartTx};
use embassy_time::{Duration, Ticker};
#[cfg(feature = "debug")]
use fmt::info;

const SAMPLE_PERIOD: Duration = Duration::from_millis(5); // 200 Hz
#[cfg(feature = "debug")]
const FORCE_LOG_EVERY_SAMPLES: u32 = 20; // 10 Hz at 200 Hz sample rate

#[embassy_executor::main]
async fn main(_spawner: Spawner) {
    let p = embassy_stm32::init(Default::default());
    let mut adc = Adc::new(p.ADC1, Resolution::BITS12);

    // C0 -> G4 force stream.
    let mut g4_uart_config = UartConfig::default();
    g4_uart_config.baudrate = FORCE_SENS_BAUD;
    let mut g4_uart = UartTx::new_blocking(p.USART1, p.PC14, g4_uart_config).unwrap();

    // Enable/disable sensors here. Disabled sensors transmit 0.
    const SENSOR_ENABLED: [bool; FORCE_SENSOR_COUNT] =
        [true, true, true, true, true, true, true, true, true, true];

    // Fill channel slots by canonical packet indices from banana_hand_common.
    let mut channels_by_slot: [Option<AnyAdcChannel<_>>; FORCE_SENSOR_COUNT] =
        [const { None }; FORCE_SENSOR_COUNT];
    channels_by_slot[FORCE_SENSOR_INDEX_IDX] = Some(p.PA0.degrade_adc());
    channels_by_slot[FORCE_SENSOR_MIDDLE_IDX] = Some(p.PA1.degrade_adc());
    channels_by_slot[FORCE_SENSOR_RING_IDX] = Some(p.PA2.degrade_adc());
    channels_by_slot[FORCE_SENSOR_PINKY_IDX] = Some(p.PA3.degrade_adc());
    channels_by_slot[FORCE_SENSOR_THUMB_IDX] = Some(p.PA8.degrade_adc());
    channels_by_slot[FORCE_SENSOR_PALM_1_IDX] = Some(p.PA4.degrade_adc());
    channels_by_slot[FORCE_SENSOR_PALM_2_IDX] = Some(p.PA5.degrade_adc());
    channels_by_slot[FORCE_SENSOR_PALM_3_IDX] = Some(p.PA6.degrade_adc());
    channels_by_slot[FORCE_SENSOR_PALM_4_IDX] = Some(p.PA7.degrade_adc());
    channels_by_slot[FORCE_SENSOR_PALM_5_IDX] = Some(p.PB2.degrade_adc());
    let mut channels: [AnyAdcChannel<_>; FORCE_SENSOR_COUNT] =
        channels_by_slot.map(|slot| slot.unwrap());

    let mut readings: [u16; FORCE_SENSOR_COUNT] = [0; FORCE_SENSOR_COUNT];
    let mut encoded: [u8; FORCE_DATA_PACKET_LEN] = [0; FORCE_DATA_PACKET_LEN];
    let mut ticker = Ticker::every(SAMPLE_PERIOD);
    #[cfg(feature = "debug")]
    let mut sample_counter: u32 = 0;
    loop {
        ticker.next().await;

        for (idx, channel) in channels.iter_mut().enumerate() {
            readings[idx] = if SENSOR_ENABLED[idx] {
                adc.blocking_read(channel, SampleTime::CYCLES24_5)
            } else {
                0
            };
        }

        // Simulated force readings for debug
        // readings = [4000; FORCE_SENSOR_COUNT];

        encode_readings_unchecked(&readings, &mut encoded);

        // In embassy-stm32 v0.5.0 this TX path is effectively infallible on Result
        // (blocking_write always return Ok(()))
        let _ = g4_uart.blocking_write(&encoded);
        #[cfg(feature = "debug")]
        {
            sample_counter = sample_counter.wrapping_add(1);
            if sample_counter % FORCE_LOG_EVERY_SAMPLES == 0 {
                info!("force: {}", readings);
            }
        }
    }
}

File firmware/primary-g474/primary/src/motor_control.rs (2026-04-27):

use crate::control_config::{
    ACTUATOR_COUNT, ACTUATOR_LOOP_CONFIGS, CONTROL_DT_S, CommandInputs, ControlMode,
    DEFAULT_CONTROL_MODE, FORCE_PID_GAINS, ForceInputs, OUTPUT_DEADBAND_PERCENT,
    POSITION_PID_GAINS, PositionInputs, force_bits_to_newtons, position_bits_to_mm,
};
use crate::pid::Pid;

const RING_IDX: usize = 0;
const PINKY_IDX: usize = 1;
const THUMB_FLEX_IDX: usize = 2;
const INDEX1_IDX: usize = 3;
const MIDDLE_IDX: usize = 4;
const THUMB_REVOLVE_IDX: usize = 5;

#[derive(Clone, Copy, PartialEq, Eq)]
pub enum MotorCommand {
    Coast,
    Brake,
    MoveOut(u8),
    MoveIn(u8),
}

#[derive(Clone, Copy, PartialEq, Eq)]
pub struct MotorPwmCommand {
    pub ch1_percent: u8,
    pub ch2_percent: u8,
}

#[derive(Clone, Copy, PartialEq, Eq)]
pub struct MotorPwmOutputs {
    pub ring: MotorPwmCommand,
    pub pinky: MotorPwmCommand,
    pub thumb_flex: MotorPwmCommand,
    pub index1: MotorPwmCommand,
    pub middle: MotorPwmCommand,
    pub thumb_revolve: MotorPwmCommand,
}

#[derive(Clone, Copy, PartialEq, Eq)]
pub struct MotorOutputs {
    pub ring: MotorCommand,
    pub pinky: MotorCommand,
    pub thumb_flex: MotorCommand,
    pub index1: MotorCommand,
    pub middle: MotorCommand,
    pub thumb_revolve: MotorCommand,
}

impl MotorOutputs {
    fn from_ordered(outputs: [MotorCommand; ACTUATOR_COUNT]) -> Self {
        Self {
            ring: outputs[RING_IDX],
            pinky: outputs[PINKY_IDX],
            thumb_flex: outputs[THUMB_FLEX_IDX],
            index1: outputs[INDEX1_IDX],
            middle: outputs[MIDDLE_IDX],
            thumb_revolve: outputs[THUMB_REVOLVE_IDX],
        }
    }

    pub fn into_pwm_outputs(self) -> MotorPwmOutputs {
        MotorPwmOutputs {
            ring: self.ring.into(),
            pinky: self.pinky.into(),
            thumb_flex: self.thumb_flex.into(),
            index1: self.index1.into(),
            middle: self.middle.into(),
            thumb_revolve: self.thumb_revolve.into(),
        }
    }
}

pub struct Controller {
    position_pids: [Pid; ACTUATOR_COUNT],
    force_pids: [Pid; ACTUATOR_COUNT],
    mode: ControlMode,
}

impl Controller {
    pub fn new(position_gains: (f32, f32, f32), force_gains: (f32, f32, f32)) -> Self {
        let (pkp, pki, pkd) = position_gains;
        let (fkp, fki, fkd) = force_gains;
        Self {
            position_pids: core::array::from_fn(|_| Pid::new(pkp, pki, pkd)),
            force_pids: core::array::from_fn(|_| Pid::new(fkp, fki, fkd)),
            mode: DEFAULT_CONTROL_MODE, // Mode should always start in position. The host device is the one to switch the hand into force control mode.
        }
    }

    pub fn mode(&self) -> ControlMode {
        self.mode
    }

    pub fn set_mode(&mut self, mode: ControlMode) {
        if self.mode != mode {
            self.mode = mode;
            self.reset_all();
        }
    }

    fn reset_all(&mut self) {
        for pid in &mut self.position_pids {
            pid.reset();
        }
        for pid in &mut self.force_pids {
            pid.reset();
        }
    }

    pub fn step(
        &mut self,
        commands: &CommandInputs,
        positions: &PositionInputs,
        forces: &ForceInputs,
    ) -> MotorOutputs {
        match self.mode {
            ControlMode::Position => self.step_position(commands, positions),
            ControlMode::Force => self.step_force(commands, forces),
        }
    }

    fn step_position(
        &mut self,
        commands: &CommandInputs,
        positions: &PositionInputs,
    ) -> MotorOutputs {
        let mut outputs = [MotorCommand::Coast; ACTUATOR_COUNT];

        for (idx, actuator) in ACTUATOR_LOOP_CONFIGS.iter().copied().enumerate() {
            let setpoint_mm = position_bits_to_mm(commands.get(actuator.command));
            let feedback_mm = position_bits_to_mm(positions.get(actuator.position));
            let u = self.position_pids[idx].update(setpoint_mm, feedback_mm, CONTROL_DT_S);
            outputs[idx] = u.into();
        }

        MotorOutputs::from_ordered(outputs)
    }

    fn step_force(&mut self, commands: &CommandInputs, forces: &ForceInputs) -> MotorOutputs {
        let mut outputs = [MotorCommand::Brake; ACTUATOR_COUNT];

        for (idx, actuator) in ACTUATOR_LOOP_CONFIGS.iter().copied().enumerate() {
            let Some(force_channel) = actuator.force else {
                // Actuators without force feedback are explicitly coasted in force mode.
                outputs[idx] = MotorCommand::Coast;
                continue;
            };

            let setpoint = force_bits_to_newtons(commands.get(actuator.command));
            let feedback = force_bits_to_newtons(forces.get(force_channel));
            let u = self.force_pids[idx].update(setpoint, feedback, CONTROL_DT_S);
            outputs[idx] = u.into();
        }

        MotorOutputs::from_ordered(outputs)
    }
}

impl Default for Controller {
    fn default() -> Self {
        Self::new(POSITION_PID_GAINS, FORCE_PID_GAINS)
    }
}

impl From<f32> for MotorCommand {
    fn from(u: f32) -> Self {
        let duty = u.abs().clamp(1.0, 100.0) as u8;
        if duty < OUTPUT_DEADBAND_PERCENT {
            return MotorCommand::Brake;
        }
        if u >= 0.0 {
            MotorCommand::MoveOut(duty)
        } else {
            MotorCommand::MoveIn(duty)
        }
    }
}

impl From<MotorCommand> for MotorPwmCommand {
    fn from(cmd: MotorCommand) -> Self {
        match cmd {
            MotorCommand::Coast => Self {
                ch1_percent: 0,
                ch2_percent: 0,
            },
            MotorCommand::Brake => Self {
                ch1_percent: 100,
                ch2_percent: 100,
            },
            MotorCommand::MoveOut(duty) => Self {
                ch1_percent: 100,
                ch2_percent: 101 - duty, // MUST BE 101 SO CH2 WILL NEVER BE 0, OR ELSE MOTOR JUST COASTS
            },
            MotorCommand::MoveIn(duty) => Self {
                ch1_percent: 101 - duty, // MUST BE 101 SO CH2 WILL NEVER BE 0, OR ELSE MOTOR JUST COASTS
                ch2_percent: 100,
            },
        }
    }
}

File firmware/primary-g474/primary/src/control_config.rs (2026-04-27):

use crate::config::{COMMAND_COUNT, FORCE_COUNT, POSITION_COUNT};
use banana_hand_common::{
    FORCE_SENSOR_INDEX_IDX, FORCE_SENSOR_MIDDLE_IDX, FORCE_SENSOR_PALM_1_IDX, FORCE_SENSOR_PALM_2_IDX,
    FORCE_SENSOR_PALM_3_IDX, FORCE_SENSOR_PALM_4_IDX, FORCE_SENSOR_PALM_5_IDX, FORCE_SENSOR_PINKY_IDX,
    FORCE_SENSOR_RING_IDX, FORCE_SENSOR_THUMB_IDX,
};

pub const CONTROL_HZ: u64 = 200;
pub const CONTROL_DT_S: f32 = 1.0 / CONTROL_HZ as f32;
pub const OUTPUT_DEADBAND_PERCENT: u8 = 5;

pub const ACTUATOR_COUNT: usize = 6;

#[derive(Clone, Copy, PartialEq, Eq)]
pub enum ControlMode {
    Position,
    Force,
}

pub const DEFAULT_CONTROL_MODE: ControlMode = ControlMode::Position;

impl ControlMode {
    pub const fn from_wire(value: u8) -> Option<Self> {
        match value {
            0 => Some(Self::Position),
            1 => Some(Self::Force),
            _ => None,
        }
    }

    pub const fn to_wire(self) -> u8 {
        match self {
            Self::Position => 0,
            Self::Force => 1,
        }
    }
}

#[derive(Clone, Copy, PartialEq, Eq)]
pub enum CommandChannel {
    Ring,
    Pinky,
    ThumbFlex,
    Index1,
    Middle,
    ThumbRevolve,
}

#[derive(Clone, Copy, PartialEq, Eq)]
pub enum PositionChannel {
    Ring,
    Pinky,
    ThumbFlex,
    Index1,
    Middle,
    ThumbRevolve,
}

#[derive(Clone, Copy, PartialEq, Eq)]
#[allow(dead_code)]
pub enum ForceChannel {
    Ring,
    Pinky,
    Thumb,
    Index,
    Middle,
    Palm1,
    Palm2,
    Palm3,
    Palm4,
    Palm5,
}

#[derive(Clone, Copy)]
pub struct CommandInputs {
    pub index1: u16,
    pub middle: u16,
    pub ring: u16,
    pub pinky: u16,
    pub thumb_flex: u16,
    pub thumb_revolve: u16,
}

impl CommandInputs {
    pub fn from_raw(raw: &[u16; COMMAND_COUNT]) -> Self {
        Self {
            index1: raw[0],
            middle: raw[1],
            ring: raw[2],
            pinky: raw[3],
            thumb_flex: raw[4],
            thumb_revolve: raw[5],
        }
    }

    pub fn get(&self, channel: CommandChannel) -> u16 {
        match channel {
            CommandChannel::Ring => self.ring,
            CommandChannel::Pinky => self.pinky,
            CommandChannel::ThumbFlex => self.thumb_flex,
            CommandChannel::Index1 => self.index1,
            CommandChannel::Middle => self.middle,
            CommandChannel::ThumbRevolve => self.thumb_revolve,
        }
    }
}

#[derive(Clone, Copy)]
#[allow(dead_code)]
pub struct PositionInputs {
    pub index1: u16,
    pub middle: u16,
    pub ring: u16,
    pub pinky: u16,
    pub thumb_flex: u16,
    pub thumb_revolve: u16,
    pub index2: u16,
    pub thumb_aux: u16,
}

impl PositionInputs {
    pub fn from_raw(raw: &[u16; POSITION_COUNT]) -> Self {
        Self {
            index1: raw[0],
            middle: raw[1],
            ring: raw[2],
            pinky: raw[3],
            thumb_flex: raw[4],
            thumb_revolve: raw[5],
            index2: raw[6],
            thumb_aux: raw[7],
        }
    }

    pub fn get(&self, channel: PositionChannel) -> u16 {
        match channel {
            PositionChannel::Ring => self.ring,
            PositionChannel::Pinky => self.pinky,
            PositionChannel::ThumbFlex => self.thumb_flex,
            PositionChannel::Index1 => self.index1,
            PositionChannel::Middle => self.middle,
            PositionChannel::ThumbRevolve => self.thumb_revolve,
        }
    }
}

#[derive(Clone, Copy)]
#[allow(dead_code)]
pub struct ForceInputs {
    pub index: u16,
    pub middle: u16,
    pub ring: u16,
    pub pinky: u16,
    pub thumb: u16,
    pub palm_1: u16,
    pub palm_2: u16,
    pub palm_3: u16,
    pub palm_4: u16,
    pub palm_5: u16,
}

impl ForceInputs {
    pub fn from_raw(raw: &[u16; FORCE_COUNT]) -> Self {
        Self {
            index: raw[FORCE_SENSOR_INDEX_IDX],
            middle: raw[FORCE_SENSOR_MIDDLE_IDX],
            ring: raw[FORCE_SENSOR_RING_IDX],
            pinky: raw[FORCE_SENSOR_PINKY_IDX],
            thumb: raw[FORCE_SENSOR_THUMB_IDX],
            palm_1: raw[FORCE_SENSOR_PALM_1_IDX],
            palm_2: raw[FORCE_SENSOR_PALM_2_IDX],
            palm_3: raw[FORCE_SENSOR_PALM_3_IDX],
            palm_4: raw[FORCE_SENSOR_PALM_4_IDX],
            palm_5: raw[FORCE_SENSOR_PALM_5_IDX],
        }
    }

    pub fn get(&self, channel: ForceChannel) -> u16 {
        match channel {
            ForceChannel::Ring => self.ring,
            ForceChannel::Pinky => self.pinky,
            ForceChannel::Thumb => self.thumb,
            ForceChannel::Index => self.index,
            ForceChannel::Middle => self.middle,
            ForceChannel::Palm1 => self.palm_1,
            ForceChannel::Palm2 => self.palm_2,
            ForceChannel::Palm3 => self.palm_3,
            ForceChannel::Palm4 => self.palm_4,
            ForceChannel::Palm5 => self.palm_5,
        }
    }
}

#[derive(Clone, Copy)]
pub struct ActuatorLoopConfig {
    pub command: CommandChannel,
    pub position: PositionChannel,
    pub force: Option<ForceChannel>,
}

// Actuator order used by the control core and MotorOutputs:
// [ring, pinky, thumb_flex, index1, middle, thumb_revolve]
pub const ACTUATOR_LOOP_CONFIGS: [ActuatorLoopConfig; ACTUATOR_COUNT] = [
    ActuatorLoopConfig {
        command: CommandChannel::Ring,
        position: PositionChannel::Ring,
        force: Some(ForceChannel::Ring),
    },
    ActuatorLoopConfig {
        command: CommandChannel::Pinky,
        position: PositionChannel::Pinky,
        force: Some(ForceChannel::Pinky),
    },
    ActuatorLoopConfig {
        command: CommandChannel::ThumbFlex,
        position: PositionChannel::ThumbFlex,
        force: Some(ForceChannel::Thumb),
    },
    ActuatorLoopConfig {
        command: CommandChannel::Index1,
        position: PositionChannel::Index1,
        force: Some(ForceChannel::Index),
    },
    ActuatorLoopConfig {
        command: CommandChannel::Middle,
        position: PositionChannel::Middle,
        force: Some(ForceChannel::Middle),
    },
    ActuatorLoopConfig {
        command: CommandChannel::ThumbRevolve,
        position: PositionChannel::ThumbRevolve,
        force: None, // no force control for thumb-revolve right now
    },
];

pub const POSITION_PID_GAINS: (f32, f32, f32) = (40.0, 0.0, 0.0);
pub const FORCE_PID_GAINS: (f32, f32, f32) = (100.0, 0.0, 0.0);

pub fn position_bits_to_mm(raw: u16) -> f32 {
    const STROKE_MM: f32 = 20.0;
    const ADC_MAX_RAW: f32 = 4095.0;
    (raw as f32) * (STROKE_MM / ADC_MAX_RAW)
}

pub fn force_bits_to_newtons(raw: u16) -> f32 {
    const MAX_FORCE: f32 = 4.9;
    const ADC_MAX_RAW: f32 = 4095.0;
    (raw as f32) * (MAX_FORCE / ADC_MAX_RAW)
}

pub const fn is_valid_config() -> bool {
    COMMAND_COUNT >= 6 && FORCE_COUNT >= 10 && POSITION_COUNT >= 8
}

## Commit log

2025-12-08 arduino code
2025-12-21 Finished adding sensor reading methods. Requires hardware testing still.
2025-12-23 Added bang-bang position controller, removed old code, and fixed typos.
    [lib.rs]
2025-12-30 Fixed errors in actuator test
    [main.rs]
2026-01-19 Got force sensor reading in c0 with rest of code
2026-01-19 force control finger
2026-01-23 fix uart test
2026-01-23 adding uart_test to firmware Cargo.toml
2026-01-28 Working on all subtimers except F. I suspect there is an issue with the PAC.
    [hrtim_pwm.rs, main.rs]
2026-02-11 Add MediaPipe hand tracking (#7)
    * Init mediapipe hand tracking
    * Detect and publish hand landmarks
    * Convert hand landmarks to per-finger actuation commands
    * Update READMEs
    * Change thumb opposition calculation from thumb tip to index MCP to thumb tip to pinky MCP
2026-02-22 Add local crate for use of HRTIM1 as simple PWM channels. (#8)
    * Added hrtim_pwm_lib, still need to test on hw
    * Changed period_reg_val to use Hertz type
    * Updated main to match new period calc
    * Fixed warnings
    * Added x32 in period calc and removed panics
    * Fixed so pin deref is no longer necessary
    * Fixed period calculator and made more clear
    * Format line
    * Fixed 100% duty cycle
    [lib.rs, main.rs]
2026-03-03 experimental: Multi Motor Position Control Working (#11)
    * changing protocol to accmodate either type of message
    * working telemetry sending
    * updated ROS readme and removed redundant code
    * Got multi motor control working, check comments in uart_g4_combo main.rs for motor/pot mapping changes
    * code cleanup, accounting for index 1 (silkscreen index 1) swapped channels
    * minor change 1
    * minor change 2
    * minor change 3
    ---------
    [control_config.rs, main.rs, motor_control.rs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]
2026-03-06 Add threading for webcam frame capture to reduce latency (#14)
    * Add threading for webcam frame capture to reduce latency
    What changed:
    The main change is that _tick() no longer calls:
    ok, frame = self._cap.read()
    Instead, read() now happens in _capture_loop():
    ok, frame = self._cap.read()
    running continuously in a background thread. Then _tick() just publishes the most recent frame.
    In the previous version, the timer fired, then we read one frame, converted it, and finally publish it and repeated this loop. So camera capture speed was tied to the timer/scheduler/publish overhead.
    Now the camera thread reads continuously as fast as possible and the newest frame is alway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
2026-03-07 Revert "Add threading for webcam frame capture to reduce latency (#14)" (#15)
    This reverts commit a8b8891069f240c6f3db92f1195c75a104832268.
2026-03-08 Add FSR Visualizer Node with working fingertip heatmap functionality (#17)
    * first demo version - not tested with real FSR
    * fix alignment issues
    * updating readme and fixing ctrl-c issue
2026-03-12 Advisor Demo March 12 (#18)
    * Preliminary testing, changed rb to k8
    * got force control working on PCB
    * GOT VISION BASED TELEOPERATION WORKING
    * got uart comm working (maybe) with kinova gen3)
    * getting rid of global cargo.lock and cargo.toml, UNCOMMENTING C0 READER THREAD SPAWNING ON G4
    * fixed ordering of FSRs and added palm data for fsr visualizer
    * Implemented triple phase calibration, improved thumb tracking, added support for thumb PWM timer, fixed joint pin mapping
    * Added manual control node
    * adding min/max motor position scaling for teleop
    * small modifications for actual demo (switching index/middle fsrs, changing thumb landmarks)
    [control_config.rs, kortex_serial_bridge_node.py, main.rs]
2026-03-17 Added edge case for 0% duty cycle (#21)
2026-03-20 Added kicad files (#22)
    [Amass_XT30UPB-F.step, B10B-PHDSS.STEP, B10B-ZR.STEP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]
2026-03-20 Final Teleop and Force/Position and Safe/Regular Modes Switching (#24)
    * added ros-based switching between force and position control and also added teleop safe and regular modes
    * added current reading and publishing
    * added 3d mediapipe mapping
    * DEFAULT MODE IS REGULAR MODE NOT SAFE MODE
2026-03-20 Add unified ROS visualization package with MuJoCo sim, FSR GUI, and new hand model (#23)
    * mujoco sim initial test
    * working mujoco visualizer with teleop, centralized visualization into one package
    * replaced with new hand design
    * updating requirements.txt
    [actuator_housing.stl, actuator_piston.stl, clevis_1.stl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]
2026-03-20 Add electrical content to repo (#25)
    * Added kicad models
    * Started writing elec docs
    * Finished first draft of elec docs
    * Linked to pcb sch
    * removed old images
    * Added known flaws section
    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
2026-03-20 Grasp classification (#20)
    * Realsense depth cam reconstruction
    * Remove ground plane with RANSAC plane segmentation
    * Grasp classification model
    * Improve ground plane removal
    * Improve grasp classification model
    * Create end to end scan to grasp pipeline
    [final_object_cloud.ply, final_object_cloud_downsampled.ply, final_object_cloud_downsampled_ground_removed.ply]
2026-03-20 Mujoco sim fixes (#27)
    * mujoco sim fixes
    * foxglove heatmap extension
    * foxglove panel
    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
    [serial_bridge_node.py]
2026-03-20 added assembly guide, resources folder, links to CAD and BOM (#31)
    * updated hardware readme
    added link to CAD, BOM
    * added new folder for assembly guide
    * Update README.md
    * fixed header
    * adding assembly guide
    * changed folder name
    * Update README.md
2026-04-27 Large FW refactor (#32)
    * Moved experiment in sensing and primary folders
    * Added common code space for force data between MCUs
    * Wired in new force common code to primary and sensor fw
    * Refactoring primary control code UNTESTED
    * Created pos adc pin struct to clean old array
    * Added from into for motor command types
    * Removed swap logic in favour of simple comment
    * Board config no longer needed
    * Added current reading task and tied into telemetry
    * Added current reading task and tied into telem. Made sure to add all files lol
    * Added control mode switching
    * Fixde controller new to have default instead of using fixed gains
    * added timeout retry logic for telem sender
    * minor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
    [board_map.rs, control_config.rs, current_reader.rs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]
